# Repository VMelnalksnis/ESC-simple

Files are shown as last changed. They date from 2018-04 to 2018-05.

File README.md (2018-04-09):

# ESC-simple

## Progress

### Software
1. Working "Blink" example for V1A
2. WIP "Control" example for V1A

### Hardware
* V1A is etched, partially soldered and tested with "Blink"
* V2A is WIP; planned changes:
	* Remove unnecessary pin connections
	* Change 7805 footprint to TO-220
	* Add 5V LED
	* Add 2 test LEDs
	* Add pull-down resistor to control input
	* Add mounting holes

### Documentation
Currently only in SOFTWARE in source.

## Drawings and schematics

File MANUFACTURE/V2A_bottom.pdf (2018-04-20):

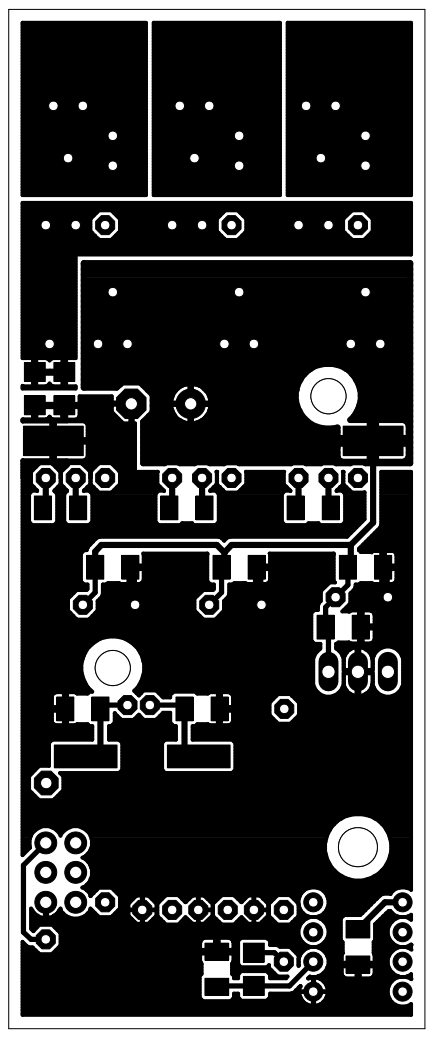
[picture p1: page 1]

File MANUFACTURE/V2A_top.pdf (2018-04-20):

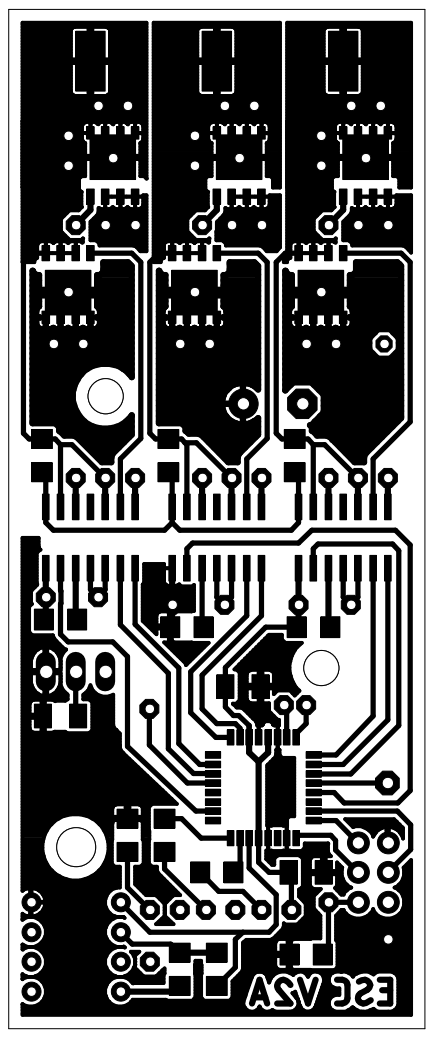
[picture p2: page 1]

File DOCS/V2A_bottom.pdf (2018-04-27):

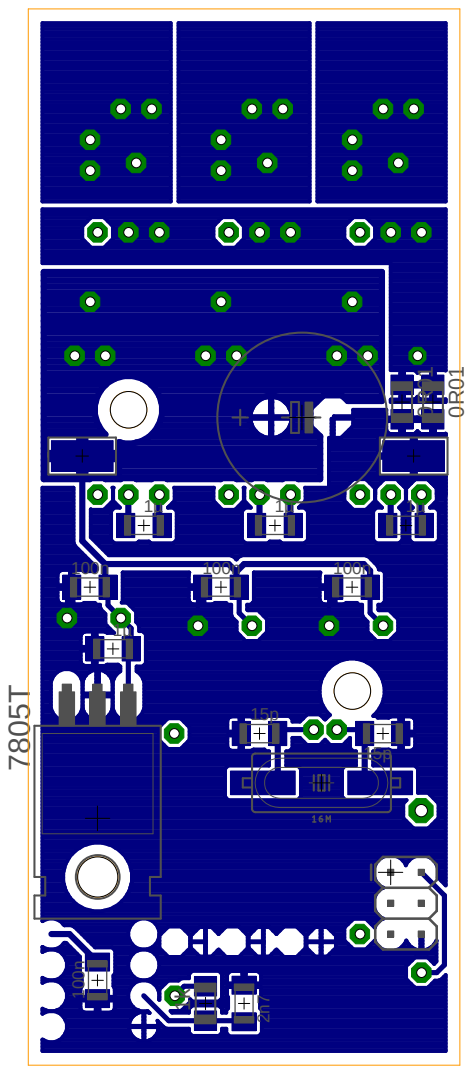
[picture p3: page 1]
0R⁰¹

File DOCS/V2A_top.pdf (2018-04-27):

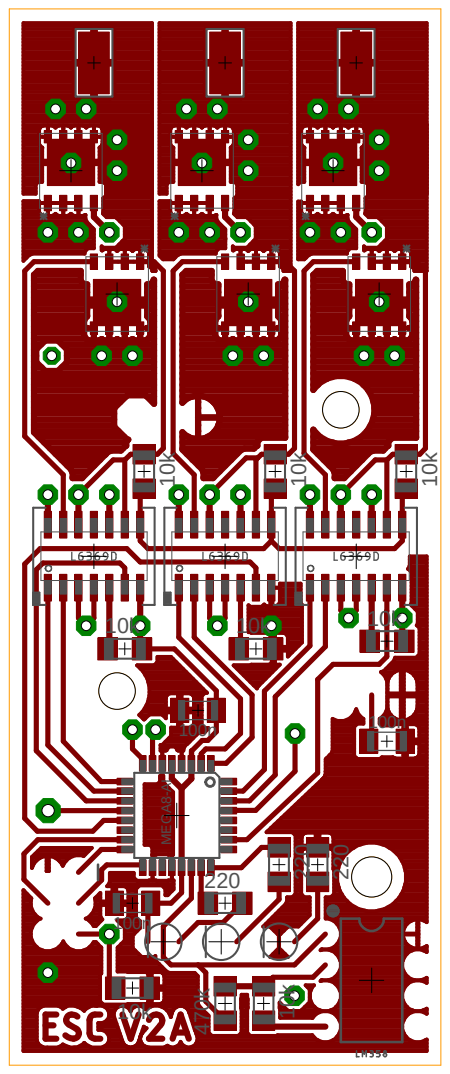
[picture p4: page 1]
100n MEGA⁸⁻AI; 10k ¹⁰k

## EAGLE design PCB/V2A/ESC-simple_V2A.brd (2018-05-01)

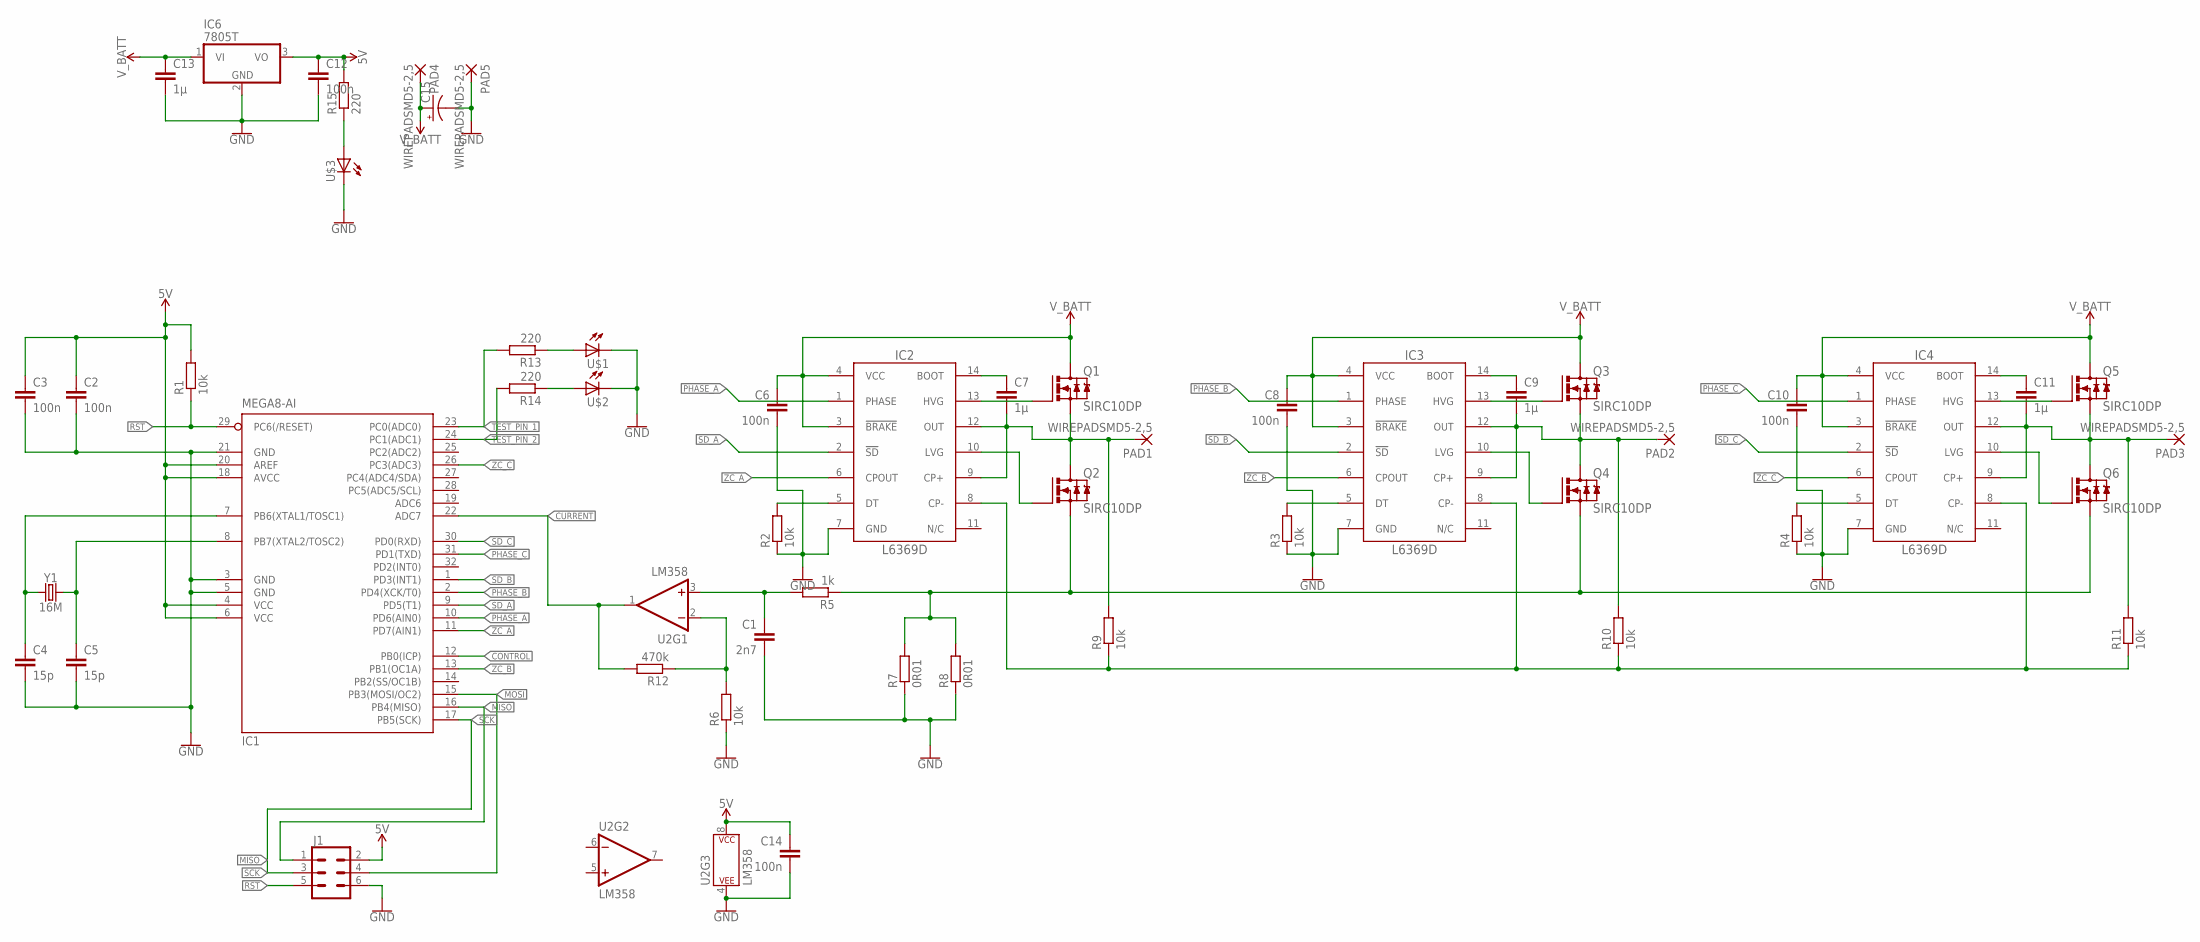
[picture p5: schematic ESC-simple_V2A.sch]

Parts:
C1: 2n7; C1206K
C2, C3, C6, C8, C10, C12, C14: 100n; C1206K
C4, C5: 15p; C1206K
C7, C9, C11, C13: 1µ; C1206K
C15: CPOL-USE5-13; E5-13
IC1: MEGA8-AI; TQFP32-08
IC2, IC3, IC4: L6369D; SO-14
IC6: 7805T; TO220H
J1: CONN_03X22X3_SILK_MALE_PTH; 2X3
PAD1, PAD2, PAD3, PAD4, PAD5: WIREPADSMD5-2,5; 5-2,5
Q1, Q2, Q3, Q4, Q5, Q6: SIRC10DP; POWERPAK_SO-8_SINGLE
R1, R2, R3, R4, R6, R9, R10, R11: 10k; R1206
R5: 1k; R1206
R7, R8: 0R01; R1206
R12: 470k; R1206
R13, R14, R15: 220; R1206
U2: LM358; DIP08
U$1, U$2, U$3: LED; 3MM_LED
Y1: 16M; HC49UP

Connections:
5V: C2.1, C3.1, C12.1, C14.1, IC1.4 (VCC), IC1.6 (VCC), IC1.18 (AVCC), IC1.20 (AREF), IC6.3 (VO), J1.2, R1.2, R15.2, U2.8 (P$V+)
A: C7.2, IC2.9 (CP+), IC2.12 (OUT), PAD1.1, Q1.1 (S), Q1.2 (S), Q1.3 (S), Q2.5 (D), Q2.6 (D), Q2.7 (D), Q2.8 (D), Q2.9 (D), R9.2
B: C9.2, IC3.9 (CP+), IC3.12 (OUT), PAD2.1, Q3.1 (S), Q3.2 (S), Q3.3 (S), Q4.5 (D), Q4.6 (D), Q4.7 (D), Q4.8 (D), Q4.9 (D), R10.2
C: C11.2, IC4.9 (CP+), IC4.12 (OUT), PAD3.1, Q5.1 (S), Q5.2 (S), Q5.3 (S), Q6.5 (D), Q6.6 (D), Q6.7 (D), Q6.8 (D), Q6.9 (D), R11.2
CONTROL: IC1.12 (PB0(ICP))
CURRENT: IC1.22 (ADC7), R12.2, U2.1 (OUT)
CURRENT_SENSE: Q2.1 (S), Q2.2 (S), Q2.3 (S), Q4.1 (S), Q4.2 (S), Q4.3 (S), Q6.1 (S), Q6.2 (S), Q6.3 (S), R5.1, R7.2, R8.2
GND: C1.2, C2.2, C3.2, C4.2, C5.2, C6.2, C8.2, C10.2, C12.2, C13.2, C14.2, C15.-, IC1.3 (GND), IC1.5 (GND), IC1.21 (GND), IC2.7 (GND), IC3.7 (GND), IC4.7 (GND), IC6.2 (GND), J1.6, PAD5.1, R2.1, R3.1, R4.1, R6.1, R7.1, R8.1, U2.4 (P$V-), U$1.C, U$2.C, U$3.C
MISO: IC1.16 (PB4(MISO)), J1.1
MOSI: IC1.15 (PB3(MOSI/OC2)), J1.4
unnamed: C7.1, IC2.14 (BOOT)
unnamed: IC2.13 (HVG), Q1.4 (G)
unnamed: IC2.10 (LVG), Q2.4 (G)
unnamed: IC3.5 (DT), R3.2
unnamed: IC2.5 (DT), R2.2
unnamed: C9.1, IC3.14 (BOOT)
unnamed: IC3.13 (HVG), Q3.4 (G)
unnamed: IC3.10 (LVG), Q4.4 (G)
unnamed: R6.2, R12.1, U2.2 (-IN)
unnamed: IC4.5 (DT), R4.2
unnamed: C11.1, IC4.14 (BOOT)
unnamed: IC4.13 (HVG), Q5.4 (G)
unnamed: IC4.10 (LVG), Q6.4 (G)
unnamed: R14.1, U$2.A
unnamed: R13.1, U$1.A
unnamed: R15.1, U$3.A
unnamed: C1.1, R5.2, U2.3 (+IN)
PHASE_A: IC1.10 (PD6(AIN0)), IC2.1 (PHASE)
PHASE_B: IC1.2 (PD4(XCK/T0)), IC3.1 (PHASE)
PHASE_C: IC1.31 (PD1(TXD)), IC4.1 (PHASE)
RST: IC1.29 (PC6(/RESET)), J1.5, R1.1
SCK: IC1.17 (PB5(SCK)), J1.3
SD_A: IC1.9 (PD5(T1)), IC2.2 (!SD)
SD_B: IC1.1 (PD3(INT1)), IC3.2 (!SD)
SD_C: IC1.30 (PD0(RXD)), IC4.2 (!SD)
TEST_PIN_1: IC1.23 (PC0(ADC0)), R13.2
TEST_PIN_2: IC1.24 (PC1(ADC1)), R14.2
V_BATT: C6.1, C8.1, C10.1, C13.1, C15.+, IC2.3 (!BRAKE), IC2.4 (VCC), IC3.3 (!BRAKE), IC3.4 (VCC), IC4.3 (!BRAKE), IC4.4 (VCC), IC6.1 (VI), PAD4.1, Q1.5 (D), Q1.6 (D), Q1.7 (D), Q1.8 (D), Q1.9 (D), Q3.5 (D), Q3.6 (D), Q3.7 (D), Q3.8 (D), Q3.9 (D), Q5.5 (D), Q5.6 (D), Q5.7 (D), Q5.8 (D), Q5.9 (D)
V_NEUTRAL: IC2.8 (CP-), IC3.8 (CP-), IC4.8 (CP-), R9.1, R10.1, R11.1
XTAL1: C4.1, IC1.7 (PB6(XTAL1/TOSC1)), Y1.1
XTAL2: C5.1, IC1.8 (PB7(XTAL2/TOSC2)), Y1.2
ZC_A: IC1.11 (PD7(AIN1)), IC2.6 (CPOUT)
ZC_B: IC1.13 (PB1(OC1A)), IC3.6 (CPOUT)
ZC_C: IC1.26 (PC3(ADC3)), IC4.6 (CPOUT)

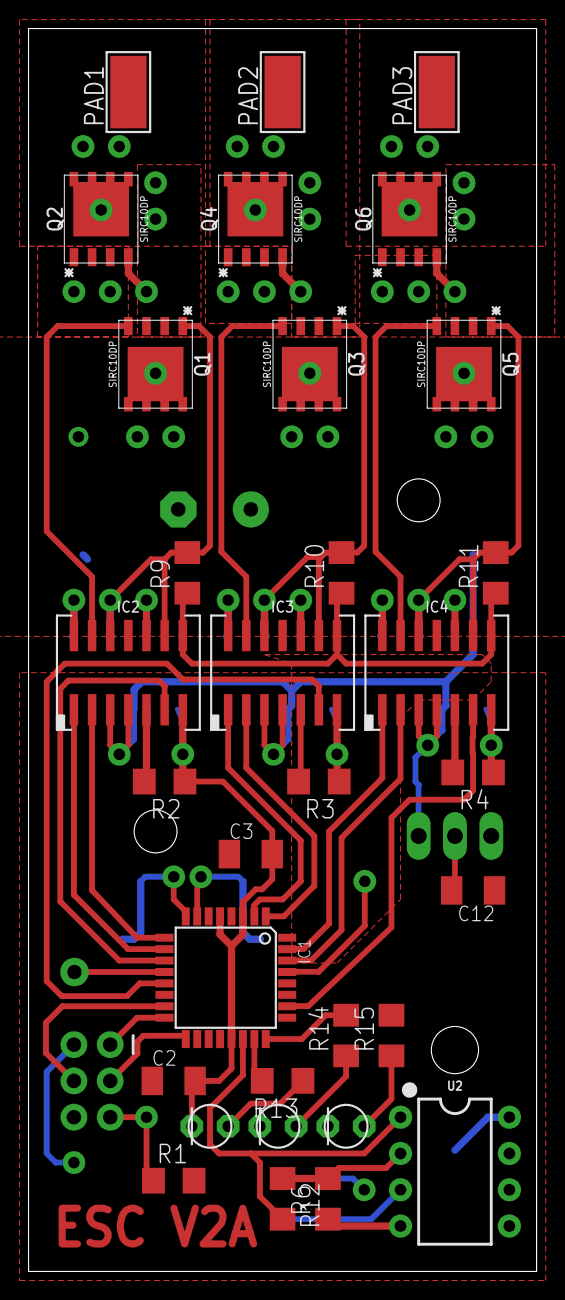
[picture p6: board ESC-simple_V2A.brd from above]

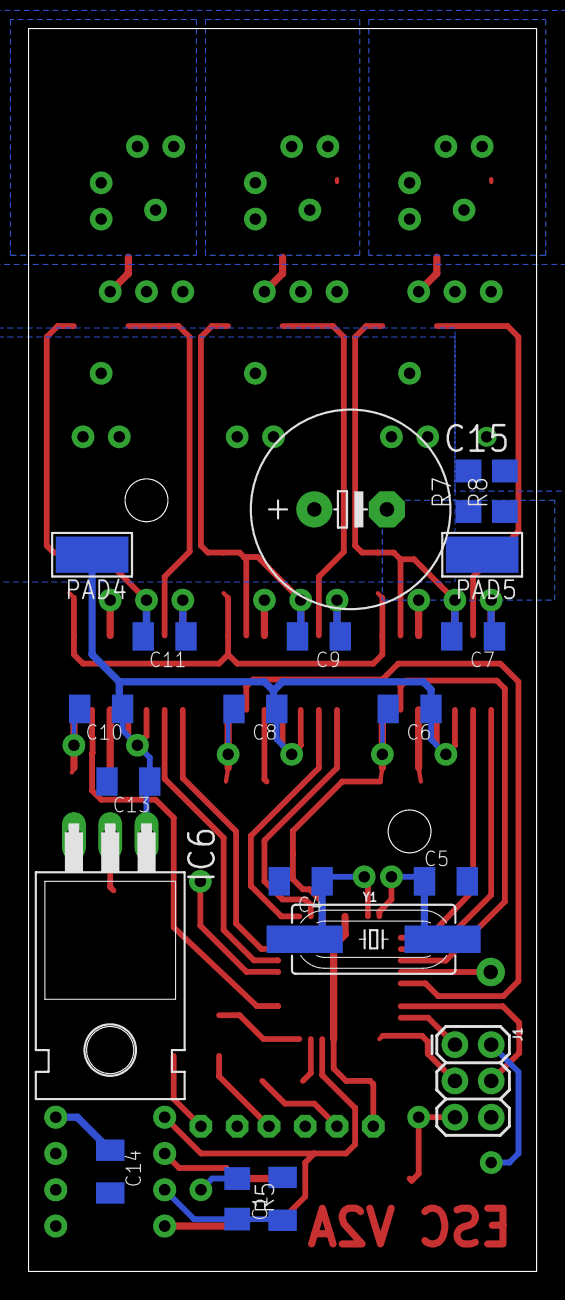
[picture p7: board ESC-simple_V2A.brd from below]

Board: 2 copper layers, 35.6 x 87.0 mm, 52 parts (20 on the bottom side), 43 nets.

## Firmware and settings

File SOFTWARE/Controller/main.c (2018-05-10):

/*
 * Controller.c
 *
 * Created: 01.05.2018 15:46:03
 * Author : Valters Melnalksnis
 */

#include "Controller.h"

volatile uint8_t current_state = 0;
volatile uint8_t ovflw_counter = 0;

const uint8_t driver_states_on[] = {	DRIVER_STATE_ON_1, DRIVER_STATE_ON_2,
										DRIVER_STATE_ON_3, DRIVER_STATE_ON_4,
										DRIVER_STATE_ON_5, DRIVER_STATE_ON_6 };
const uint8_t driver_states_off[] = {	DRIVER_STATE_OFF_1, DRIVER_STATE_OFF_2,
										DRIVER_STATE_OFF_3, DRIVER_STATE_OFF_4,
										DRIVER_STATE_OFF_5, DRIVER_STATE_OFF_6 };

/*	Time at which the current control signal began.	*/
volatile uint16_t control_start;
/*	Width of the last control signal pulse, in clock cycles.	*/
volatile uint16_t control_width;

volatile uint8_t driver_frequency;

int main(void)
{
	InitIO();
	
	/*	Initialize Timer0, which is used to control the PWM duty cycle.	*/
	/*	Disconnect compare outputs, normal mode of operation, pre-scaler of 1.	*/
	TCCR0A = 0;
	TCCR0B = (1 << CS01);
	/*	Enable output compare B, output compare B and overflow interrupt.	*/
	TIMSK0 = (1 << OCIE0B) | (1 << OCIE0A) | (0 << TOIE0);
	/*	Timer0 output compare A value; corresponds to PWM period (20kHz).	*/
	OCR0A = 50;
	/*	Timer0 output compare B value; corresponds to PWM ON width.	*/
	OCR0B = 100;
	
	/*	Initialize Timer1, which is used to measure the control signal.	*/
	/*	Disconnect compare outputs, normal mode of operation,
		enable input capture noise canceler, input capture positive edge,
		pre-scaler set to 1, disable force output compare.	*/
	TCCR1A = 0;
	TCCR1B = (1 << ICNC1) | (1 << ICES1) | (1 << CS10);
	TCCR1C = 0;
	/*	Enable interrupt capture interrupt.	*/
	TIMSK1 = (1 << ICIE1) | (0 << TOIE1);
	
	/*	Initialize Timer2, which is used to control commutation frequency.	*/
	/*	Pre-scaler 1024.	*/
	TCCR2A = 0;
	TCCR2B = (1 << CS22) | (1 << CS21) | (1 << CS20);
	/*	Enable overflow interrupt.	*/
	TIMSK2 = (1 << TOIE2);

	/*	Enable global interrupts.	*/
	sei();

	while (1)
	{
		if (control_width < 16000)
		{
			TEST_PORT = 0;
		} 
		else if (control_width < 32000)
		{
			TEST_PORT = 1;
		}
		else
		{
			TEST_PORT = (1 << TEST_PIN_2) | (1 << TEST_PIN_1);
		}
	}
}

/*
 *	Initialize all the digital and analog inputs and outputs.
 */
void InitIO()
{
	/*	Set CONTROL and ZC_B as inputs.	*/
	DDRB = 0;
	/*	Disable pull-up resistors for CONTROL and ZC_B.	*/
	PORTB = 0;

	/*	Set test pins as outputs, ZC_C as input.	*/
	DDRC = (0 << ZC_C_PIN) | (1 << TEST_PIN_2) | (1 << TEST_PIN_1);
	/*	Set test pins to LOW, disable pull-up resistor on ZC_C.	*/
	PORTC = (0 << ZC_C_PIN) | (0 << TEST_PIN_2) | (0 << TEST_PIN_1);

	/*	Set driver control pins as outputs, ZC_A as input.	*/
	DDRD =	(0 << ZC_A_PIN) |
			(1 << PHASE_A) | (1 << SD_A) |
			(1 << PHASE_B) | (1 << SD_B) |
			(1 << PHASE_C) | (1 << SD_C);
	/*	Set driver control pins to LOW, disable pull-up resistor on ZC_A.	*/
	PORTD =	(0 << ZC_A_PIN) |
			(0 << PHASE_A) | (0 << SD_A) |
			(0 << PHASE_B) | (0 << SD_B) |
			(0 << PHASE_C) | (0 << SD_C);

	/*	AREF as voltage reference, left adjusted, ADC7 (current).	*/
	ADMUX = (1 << ADLAR) | (0 << MUX3) | (1 << MUX2) | (1 << MUX1) | (1 << MUX0);
	/*	ADC disabled, start conversion, disable interrupt, pre-scaler 128.	*/
	ADCSRA =	(0 << ADEN) | (1 << ADSC) | (0 << ADATE) | (0 << ADIE) |
				(1 << ADPS2) | (1 << ADPS1) | (1 << ADPS0);
	/*	Disable analog comparator multiplexer, free running mode.	*/
	ADCSRB = 0;
}

/*
 *	Timer1 Input Capture interrupt service routine - executed when the select edge is
 *	detected on the input capture pin. Used to measure the positive pulse width of the
 *	input control signal that determines the target speed.
 *
 *	control_width:
 *	60 cycles (3.75µs) if rising edge, 70 cycles (4.375µs) if falling edge.
 *
 *	driver_frequency:
 *	76 cycles (4.75µs) if rising edge, 121 cycles (7.5625µs) if falling edge.
 */
ISR(TIMER1_CAPT_vect)
{
	/*	Read the captured value first so it isn't overwritten.	*/
	uint16_t temp = ICR1;

	if ((TCCR1B & (1 << ICES1)) == 0)
	{
		/*	Falling edge.	*/
		/*	Save the pulse width.	*/
		control_width = temp - control_start;
		if (control_width < CTRL_WIDTH_MIN)
		{
			control_width = CTRL_WIDTH_MIN;
		}
		else if(control_width > CTRL_WIDTH_MAX)
		{
			control_width = CTRL_WIDTH_MAX;
		}
		driver_frequency = (control_width - 16000) / 178 + 5;
		OCR0A = driver_frequency;
	}

	/*	Save the pulse start time.	*/
	control_start = temp;
	/*	Toggle the input capture edge, so the opposite edge is captured next.	*/
	TCCR1B ^= (1 << ICES1);
	/*	Clear the Input Capture Flag so the next edge can be captured.	*/
	TIFR1 = (1 << ICF1);
}

ISR(TIMER0_COMPB_vect)
{
	/*	New PWM cycle, set driver controls to equal to current state ON.	*/
	DRIVER_PORT = driver_states_on[current_state];
	/*	Reset the timer.	*/
	TCNT0 = 0;
}

ISR(TIMER0_COMPA_vect)
{
	/*	Set driver controls equal to current state OFF.	*/
	DRIVER_PORT = driver_states_off[current_state];
}

ISR(TIMER2_OVF_vect)
{
	ovflw_counter++;
	
	if (ovflw_counter >= 10)
	{
		
	} 
	else
	{
	}
	
	if (current_state == 6)
	{
		current_state = 0;
	} 
	else
	{
		current_state++;
	}
}

/*
 *	Analog Digital Converter interrupt service routine - executed when the ADC has
 *	finished a conversion. Variable control_start gets zeroed each time TIMER1_CAPT_vect
 *	is executed if ADC interrupt is enabled and this ISR isn't present, thus it isn't
 *	possible to measure control pulse width. TODO - check if it is the same outside of
 *	simulation.
 */
/*ISR(ADC_vect)
{

}*/

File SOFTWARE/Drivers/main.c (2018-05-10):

/*
 *	main.c
 *
 *	Created	: 08.04.2018 14:47:38
 *	Author	: Valters Melnalksnis
 *	PCB		: V1A
 */

#include <avr/io.h>
#include <avr/interrupt.h>
#include <util/delay.h>

// PB1:
//	-) PCINT1	- Pin Change Interrupt 1
//	-) OC1A		- Timer/Counter1 Output Compare Match A Output
// PB2:
//	-) PCINT2	- Pin Change Interrupt 2
//	-) OC1B		- Timer/Counter1 Output Compare Match B Output
//	-) SS		- SPI Bus Master Slave select

#define V2A

#ifdef V1A

#define TEST_PIN_1		PINB1
#define TEST_PIN_2		PINB2
#define TEST_DDR		DDRB
#define TEST_PORT		PORTB

#endif

#ifdef V2A

#define TEST_PIN_1		PINC0
#define TEST_PIN_2		PINC1
#define TEST_DDR		DDRC
#define TEST_PORT		PORTC

#endif

/*	Pins used to control the 3 half-bridge drivers.	*/
#define DRIVER_DDR		DDRD
#define DRIVER_PORT		PORTD
#define SD_C			PIND0
#define PHASE_C			PIND1
#define SD_B			PIND3
#define PHASE_B			PIND4
#define SD_A			PIND5
#define PHASE_A			PIND6

#define DRIVER_STATE_1	((1 << SD_A) | (1 << PHASE_A) | (1 << SD_B))
#define DRIVER_STATE_2	((1 << SD_A) | (1 << PHASE_A) | (1 << SD_C))
#define DRIVER_STATE_3	((1 << SD_B) | (1 << PHASE_B) | (1 << SD_C))
#define DRIVER_STATE_4	((1 << SD_B) | (1 << PHASE_B) | (1 << SD_A))
#define DRIVER_STATE_5	((1 << SD_C) | (1 << PHASE_C) | (1 << SD_A))
#define DRIVER_STATE_6	((1 << SD_C) | (1 << PHASE_C) | (1 << SD_B))

const uint8_t driver_states[] = {	DRIVER_STATE_1, DRIVER_STATE_2, DRIVER_STATE_3,
									DRIVER_STATE_4, DRIVER_STATE_5, DRIVER_STATE_6 };
volatile uint8_t current_state = 0;

char enableLED = 1;
int counter = 1;

volatile uint16_t tot_overflow;


int main(void)
{
	// Set test pins as outputs.
	TEST_DDR = (1 << TEST_PIN_1) | (1 << TEST_PIN_2);
	// Set outputs to LOW.
	TEST_PORT = (1 << TEST_PIN_1) | (0 << TEST_PIN_2);
	
	/*	Set driver control pins as outputs.	*/
	DRIVER_DDR = (1 << SD_C) | (1 << PHASE_C) | (1 << SD_B) | (1 << PHASE_B) | (1 << SD_A) | (1 << PHASE_A);
	/*	Close phase A high-side MOSFET and phase B low-side MOSFET.	*/
	DRIVER_PORT = 0;
	
	// Initialize timer
	// Setup Timer0 in normal mode of operation and 1024 prescaler
	TCCR0A = 0;
	TCCR0B = (0 << CS02) | (0 << CS01) | (1 << CS00);
	// Enable Overflow Interrupt Enable
	TIMSK0 = (1 << TOIE0);
	// Initialize counter
	TCNT0 = 0;
	sei();

	while (1)
	{
		if (tot_overflow >= counter)
		{
			TEST_PORT ^= (1 << TEST_PIN_1) | (1 << TEST_PIN_2);
			tot_overflow = 0;
			counter++;
			if (counter >= (UINT16_MAX - 1))
			{
				counter = 1;
			}
		}
	}
}

ISR(TIMER0_OVF_vect)
{
	tot_overflow++;
	
	if (current_state == 5)
	{
		current_state = 0;
	}
	else
	{
		current_state++;
	}
	
	DRIVER_PORT = driver_states[current_state];
}

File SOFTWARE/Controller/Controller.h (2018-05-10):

/*
 * Controller.h
 *
 * Created: 01.05.2018 15:47:08
 *  Author: Valters Melnalksnis
 */

/*	Pin map V2A
 *	12	PB0		ICP		IN	Control signal
 *	13	PB1		PCINT0	IN	Zero crossing Phase B (ZC_B)
 *	14	PB2		-		-	N/C
 *	15	PB3		MOSI	-	ISP
 *	16	PB4		MISO	-	ISP
 *	17	PB5		SCK		-	ISP
 *	7	PB6		XTAL1	-	Crystal
 *	8	PB7		XTAL2	-	Crystal
 *
 *	23	PC0		-		OUT	Test/status LED 1
 *	24	PC1		-		OUT	Test/status LED 2
 *	25	PC2		-		-	N/C
 *	26	PC3		PCINT11	IN	Zero crossing Phase C (ZC_C)
 *	27	PC4		-		-	N/C
 *	28	PC5		-		-	N/C
 *	29	PC6		RESET	-	ISP
 *
 *	30	PD0		-		OUT	Shutdown signal Phase C (SD_C)
 *	31	PD1		-		OUT	Phase signal Phase C (PHASE_C)
 *	32	PD2		-		-	N/C
 *	1	PD3		-		OUT	Shutdown signal Phase B (SD_B)
 *	2	PD4		-		OUT	Phase signal Phase B (PHASE_B)
 *	9	PD5		-		OUT Shutdown signal Phase A (SD_A)
 *	10	PD6		-		OUT	Phase signal Phase A (PHASE_A)
 *	11	PD7		PCINT23	IN	Zero crossing Phase A (ZC_A)
 *
 *	19	ADC6	-		-	N/C
 *	22	ADC7	ADC		IN	Current measurement
 */

#include <avr/io.h>
#include <avr/interrupt.h>

/*	Pins connected to LEDs used for testing and status indication.	*/
#define TEST_PIN_1		PINC0
#define TEST_PIN_2		PINC1
/*	DDR associated with the test/status pins.*/
#define TEST_DDR		DDRC
/*	PORT register associated with the test/status pins.	*/
#define TEST_PORT		PORTC

/*	Pins used to control the 3 half-bridge drivers.	*/
#define SD_C			PIND0
#define PHASE_C			PIND1
#define SD_B			PIND3
#define PHASE_B			PIND4
#define SD_A			PIND5
#define PHASE_A			PIND6
/*	DDR associated with the driver control pins.	*/
#define DRIVER_DDR		DDRD
/*	PORT register associated with the driver control pins.	*/
#define DRIVER_PORT		PORTD

/*	DRIVER_PORT states during each commutation state (ON).	*/
#define DRIVER_STATE_ON_1	((1 << SD_A) | (1 << PHASE_A) | (1 << SD_B))
#define DRIVER_STATE_ON_2	((1 << SD_A) | (1 << PHASE_A) | (1 << SD_C))
#define DRIVER_STATE_ON_3	((1 << SD_B) | (1 << PHASE_B) | (1 << SD_C))
#define DRIVER_STATE_ON_4	((1 << SD_B) | (1 << PHASE_B) | (1 << SD_A))
#define DRIVER_STATE_ON_5	((1 << SD_C) | (1 << PHASE_C) | (1 << SD_A))
#define DRIVER_STATE_ON_6	((1 << SD_C) | (1 << PHASE_C) | (1 << SD_B))

/*	DRIVER_PORT states during each commutation state (OFF).	*/
#define DRIVER_STATE_OFF_1	((1 << SD_A) | (1 << PHASE_A) | (1 << SD_B) | (1 << PHASE_B))
#define DRIVER_STATE_OFF_2	((1 << SD_A) | (1 << SD_C))
#define DRIVER_STATE_OFF_3	((1 << SD_B) | (1 << PHASE_B) | (1 << SD_C) | (1 << PHASE_C))
#define DRIVER_STATE_OFF_4	((1 << SD_B) | (1 << SD_A))
#define DRIVER_STATE_OFF_5	((1 << SD_C) | (1 << PHASE_C) | (1 << SD_A) | (1 << PHASE_A))
#define DRIVER_STATE_OFF_6	((1 << SD_C) | (1 << SD_B))

/*	Pin used to detect zero crossing for phase A. PCINT23.	*/
#define ZC_A_DDR		DDRD
#define ZC_A_PORT		PORTD
#define ZC_A_PINS		PIND
#define ZC_A_PIN		PIND7
#define ZC_A_INT		PCINT23

/*	Pin used to detect zero crossing for phase B. PCINT0.	*/
#define ZC_B_DDR		DDRB
#define ZC_B_PORT		PORTB
#define ZC_B_PINS		PINB
#define ZC_B_PIN		PINB0
#define ZC_B_INT		PCINT0

/*	Pin used to detect zero crossing for phase C. PCINT11.	*/
#define ZC_C_DDR		DDRC
#define ZC_C_PORT		PORTC
#define ZC_C_PINS		PINC
#define ZC_C_PIN		PINC3
#define ZC_C_INT		PCINT11

/*	Minimum control signal pulse width (1ms).	*/
#define CTRL_WIDTH_MIN	16000
/*	Maximum control signal pulse width (2ms).	*/
#define CTRL_WIDTH_MAX	32000

/*	Array containing driver commutation states in order.	*/
extern const uint8_t driver_states_on[6];
extern const uint8_t driver_states_off[6];

void InitIO(void);
void BlindStart(void);

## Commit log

2018-04-08 Added PCB/V1A
    [ESC-simple.brd, ESC-simple.sch]
2018-04-08 Added PCB/V2A
    [ESC-simple_V1A.brd, ESC-simple_V1A.sch, ESC-simple_V2A.brd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]
2018-04-08 Missed this
    [ESC-simple.brd]
2018-04-08 Added SOFTWARE/Control
    [ESC-simple_V2A.brd]
2018-04-20 V2A (#1)
    * Edited
    * replaced paths
    * V2A Final
    V2A already etched.
    [ESC-simple_V2A.brd, ESC-simple_V2A.sch]
2018-04-27 Added docs, updated Blink for V2A
    [ESC-simple_V2A.brd]
2018-05-01 Updated EAGLE
    [ESC-simple_V2A.brd]

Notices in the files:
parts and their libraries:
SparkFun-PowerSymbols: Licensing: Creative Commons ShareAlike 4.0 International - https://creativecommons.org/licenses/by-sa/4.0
